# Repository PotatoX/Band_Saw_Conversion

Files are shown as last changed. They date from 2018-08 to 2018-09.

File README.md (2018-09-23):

# Band_Saw_Conversion

## Summary
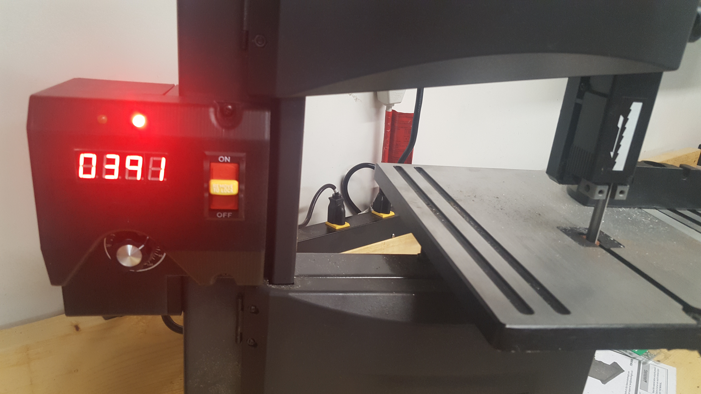
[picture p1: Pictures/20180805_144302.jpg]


Recently I needed (had an excuse to get) a band saw capable of cutting metal for a few of my projects. As with most of my projects/hobbies there are a number of outcomes I seek:

* Cheap
* Technical
* Build
* Learn

To this end I started shopping around to acquire a band saw as cheap as possible as it would only be used on a limited basis for hobby work. I need the saw to be able to cut metal and fit a small foot print on my bench. I wanted the saw to be vertical in order to minimize the space consumed as my bench and garage space is at a premium at this point.

With these constraints in mind I set my sights on a Harbor Freight 1/3 HP 9 in Benchtop Band Saw. I caught it on sale a Harbor Freight (w/ coupon) for right around $100. Similar saws can be found at your local big box stores.

Using this basic frame and some upgrades I have been able to convert this wood cutting vertical band saw to a metal cutting type with speed control and FPS display.

I now have a small band saw capable of cutting metal, wood, plastic, etc. that fits on the corner of my bench.

This project encompass the conversion and in indented to share the process with other makers. If you have questions, need additional details, or see any bugs please let me know.

The entire project can be found on [GitHub](https://github.com/PotatoX/Band_Saw_Conversion/). Consider contributing and making it even better if you happen to create other customizations.

Additionally, I will list parts used in this project on my [OpenBazzar store](https://openbazaar.com/store/QmVFRGwApdcef56Be7FPXnXQaB79rYrve3otFsrWvSwbAu).

## Design Choices
Thnking ack thrpugh the steps taken from the begining to end; a text book design process was not followed, rather a development and refine!emt from blade to display.

### The Blade
There the first choice was to find a blade that fit and was capable of cutting metalss (steel). By default the saw comes equiped woth a wood cutting 62in blade, carbon steel, 7 Teeth per Inch (*TPI*), 1/8in wide. I had found a couple of reports online that indicate success cutting plastic and aluminium, so long as a gentle touch was used. clearly the default blade had no chance of taking on steels.

Therefore the search began for a suitable bimetal blade. Most of my local stores carried various blades, some bimetal, but none in the 62in size. 62in appears to be a bit of a *custom* size. when local stores fail Amazon.com often saves the day. After scrolling though lists of blades I was able to to find a suitable blade; 62in, bimetal, 1/2in, 14 TPI.

[Imachinist S621214 62-inch X 1/2-inch X 14 TPI Bi-metal Band Saw Blades](https://www.amazon.com/gp/product/B010G9IJG6)

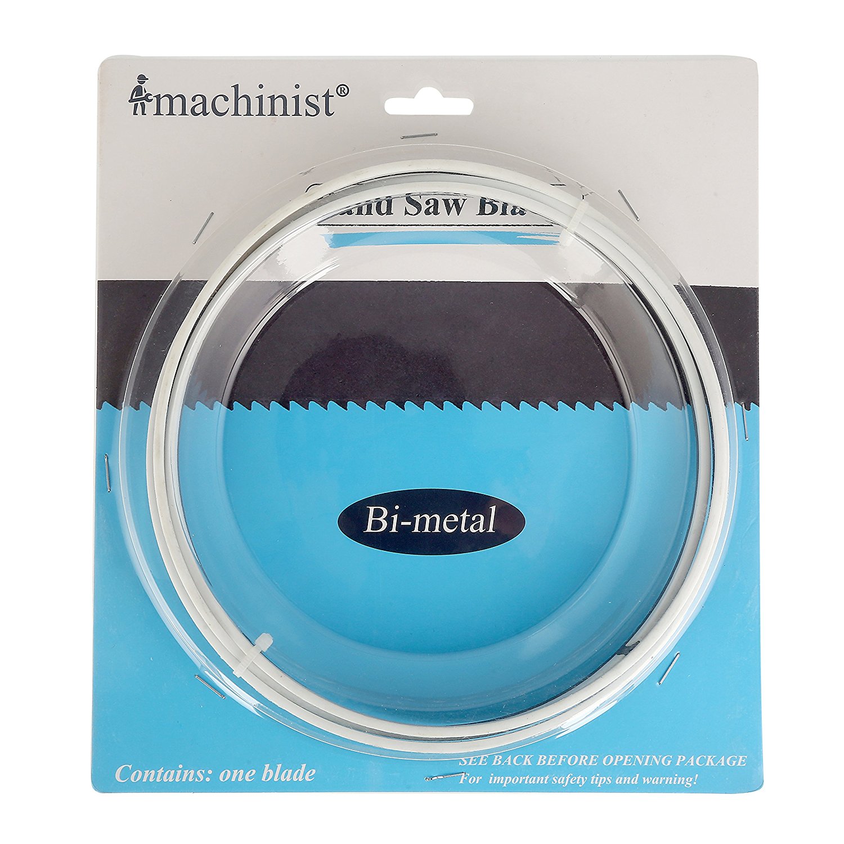
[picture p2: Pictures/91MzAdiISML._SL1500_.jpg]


The next challenge was to find a way to drive the blade @ ~300 FPM for Steel, 600ish FPM for Aluminum, and 2000 FPM for Wood. Looking at the stock motor it was designed to drive the blade at 2460 FPM and is not adjustable. Further the motor is an induction motor which can not be speed controlled without a frequency drive, and even with one, would loose power proportional to the reduction in frequency; meaning at slow speeds is would lose power.

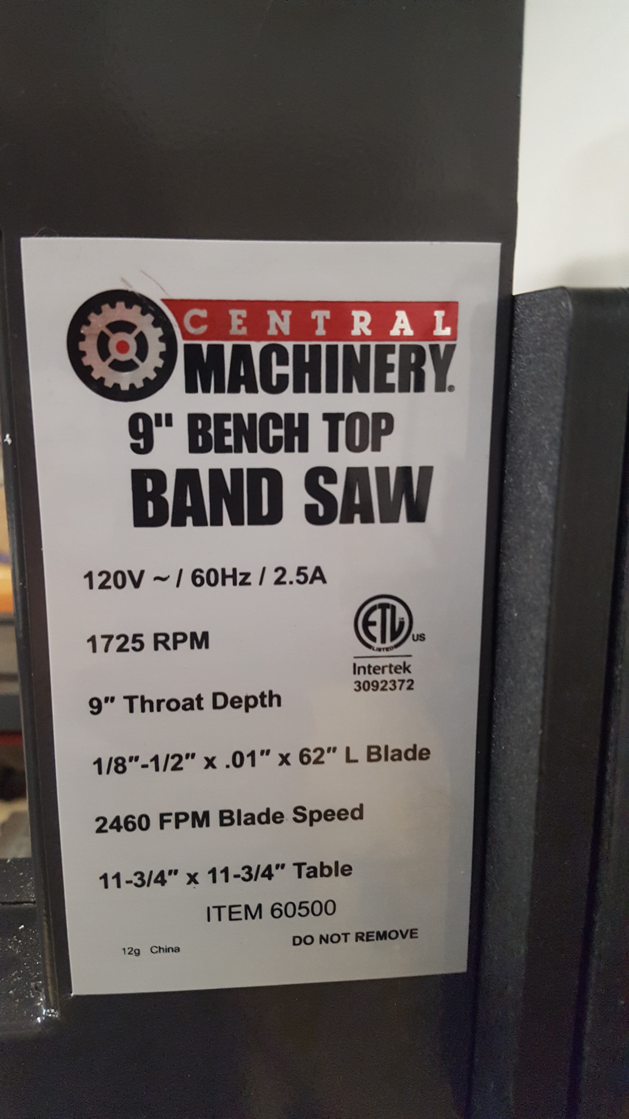
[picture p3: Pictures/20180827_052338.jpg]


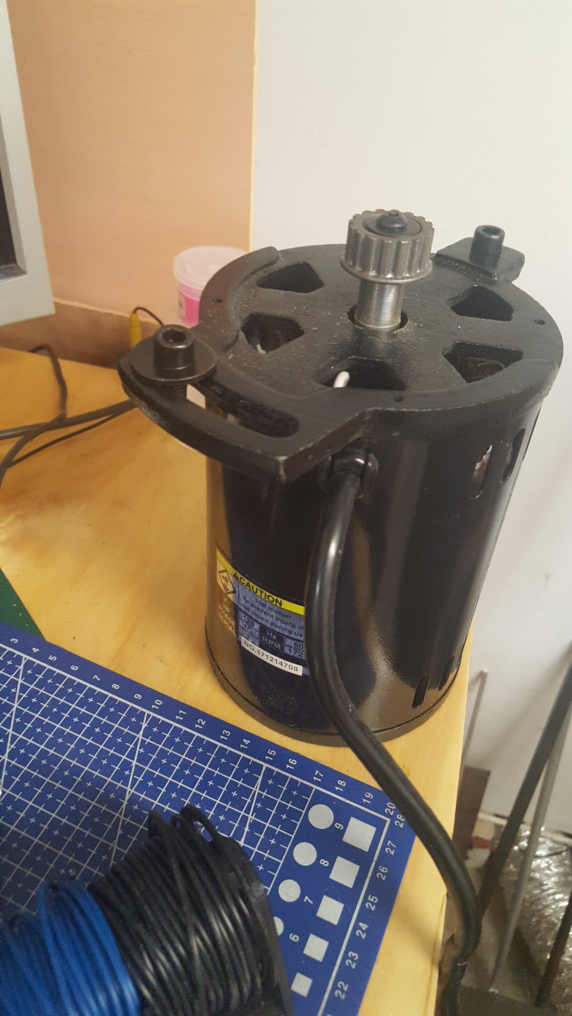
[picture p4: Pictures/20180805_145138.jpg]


Therefore, a SCR controlled DC motor setup was needed. Given the *Cheap* requirement I scrubed ebay for a cheap DC motor. I found that used DC motors from tredmills seem to be abundent and are therefore reasonably priced. I found mine for ~$30.

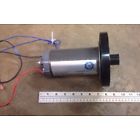
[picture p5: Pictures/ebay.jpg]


A small bracket had to be made to adapat the motor to the band saw frame

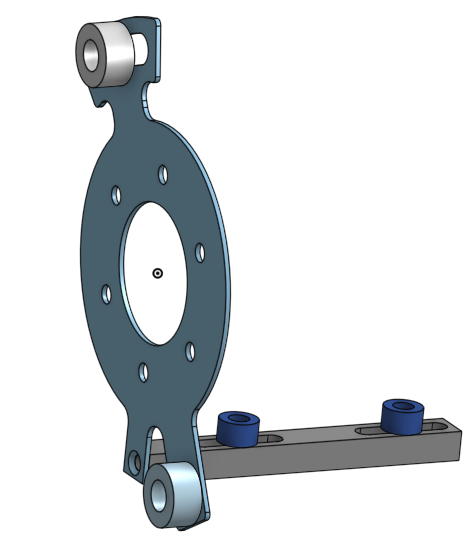
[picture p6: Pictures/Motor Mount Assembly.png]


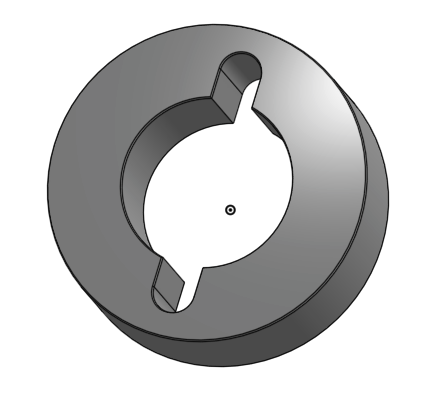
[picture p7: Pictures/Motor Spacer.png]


In order to control the motor I found a generic SCR speed control. The exact feature of the SCR were not necessary to specify other than it needed to be able to handle sufficient power. 4000W was probably over kill, but rather more than not enough, and given the price for smaller units was roughly the same, this did the trick.

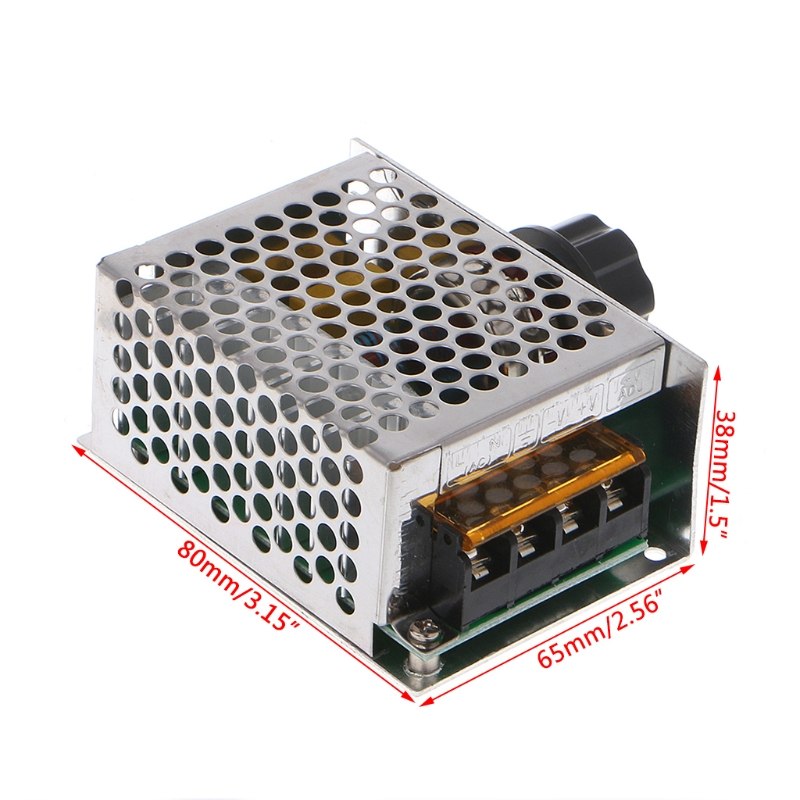
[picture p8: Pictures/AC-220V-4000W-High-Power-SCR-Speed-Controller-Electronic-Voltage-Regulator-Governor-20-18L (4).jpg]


The SCR needed a couple of mods to fine tune the upper and lower speed bounds. This is expanded on more in in the electronics section.

In order to install the motor I had a to get small belt pully mate to the motor.

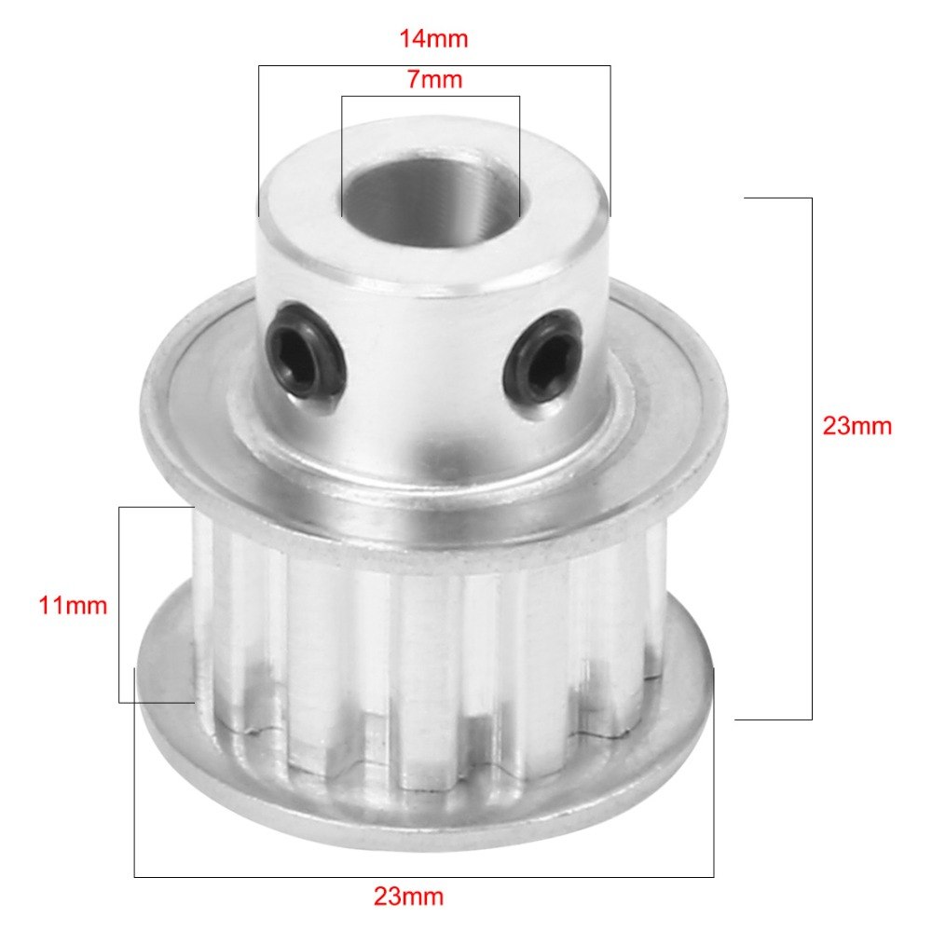
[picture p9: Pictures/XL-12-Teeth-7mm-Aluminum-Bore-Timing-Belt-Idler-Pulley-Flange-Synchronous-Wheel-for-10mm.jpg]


I then needed an clean way to mount the SCR on the frame which led to the need to design an enclosure to house and mount the SCR.

I figured, if I am going to make a custom enclosure might as well make a display to disply the FPM of the blade; I mean I've come this far, why not.

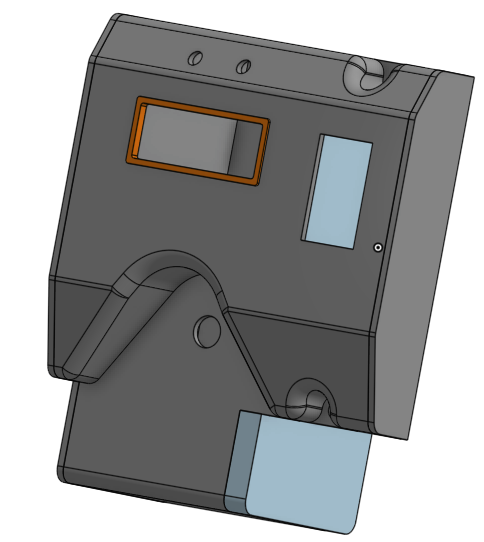
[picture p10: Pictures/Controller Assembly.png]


Lastely I designed a small board which reads a hall sensor on the back of the motor, then converts the motor shaft speed to FPM, and displays this on a small 7-Segment output. 

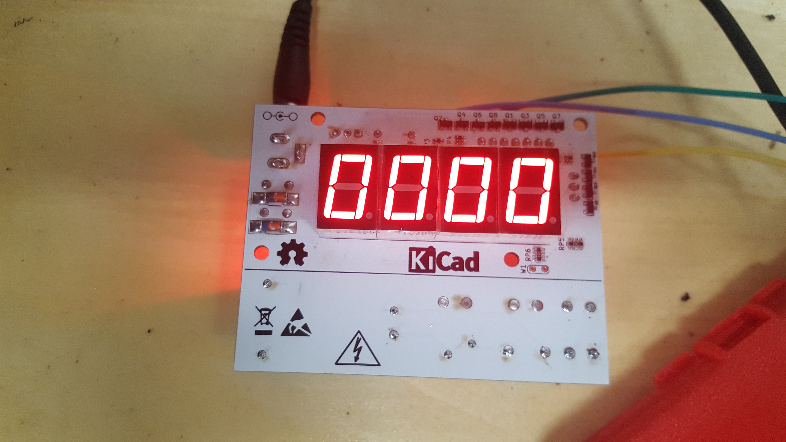
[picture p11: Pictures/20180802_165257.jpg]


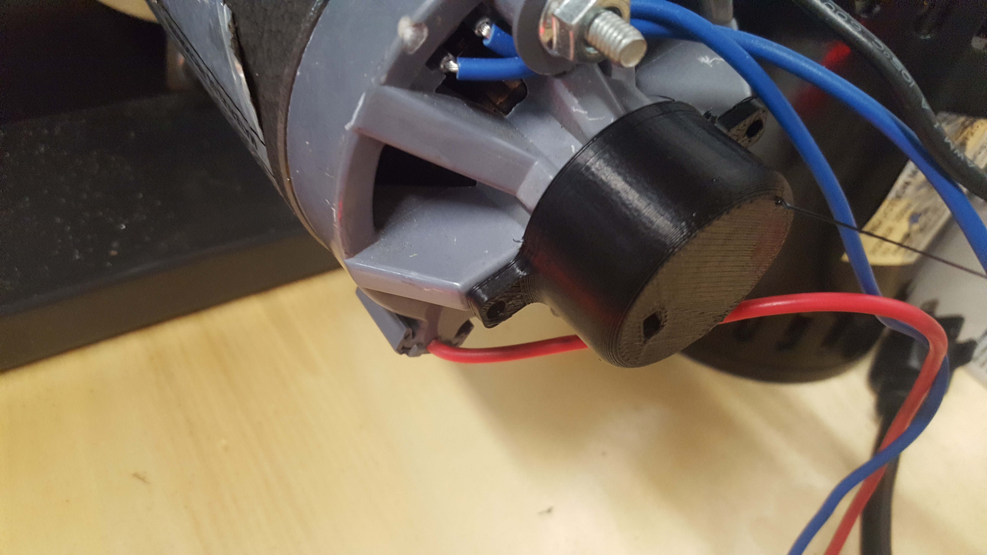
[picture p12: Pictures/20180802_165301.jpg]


## The Physical Form

### Hardware
The enclosure has been modeled in Onshape, source files can be found [here](https://cad.onshape.com/documents/ca0881e1177c075414a017b7/w/e514d8a98751ae0bca0296ff/e/90af0d38bd02678226dfc615).

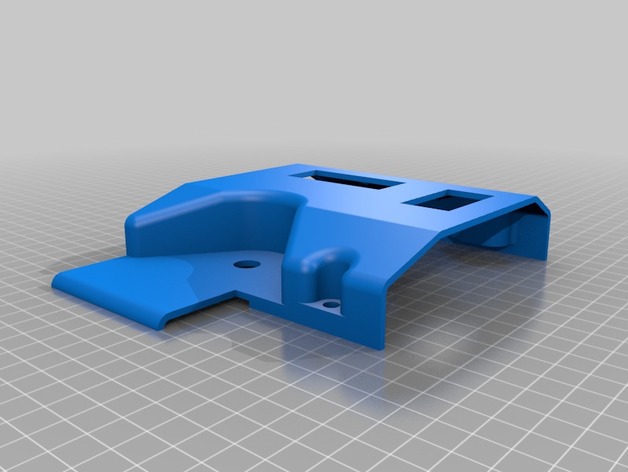
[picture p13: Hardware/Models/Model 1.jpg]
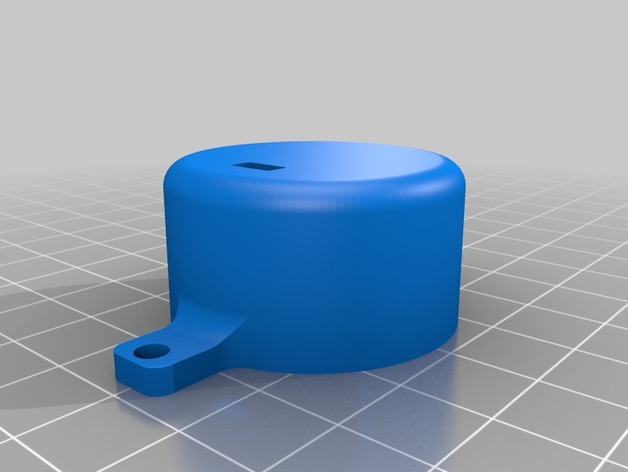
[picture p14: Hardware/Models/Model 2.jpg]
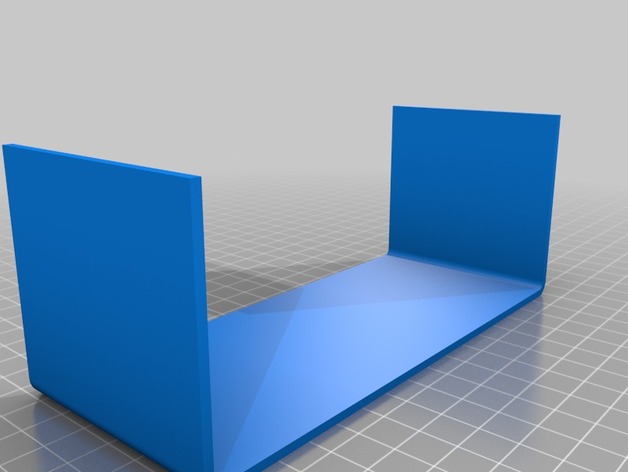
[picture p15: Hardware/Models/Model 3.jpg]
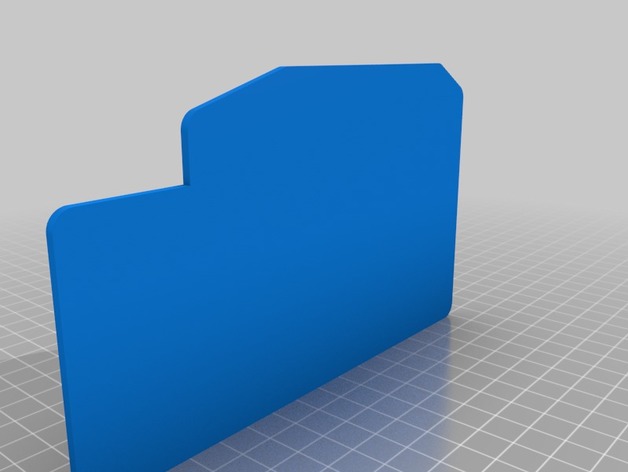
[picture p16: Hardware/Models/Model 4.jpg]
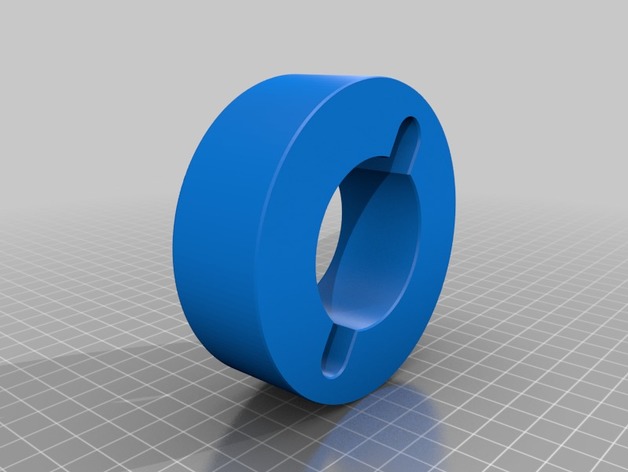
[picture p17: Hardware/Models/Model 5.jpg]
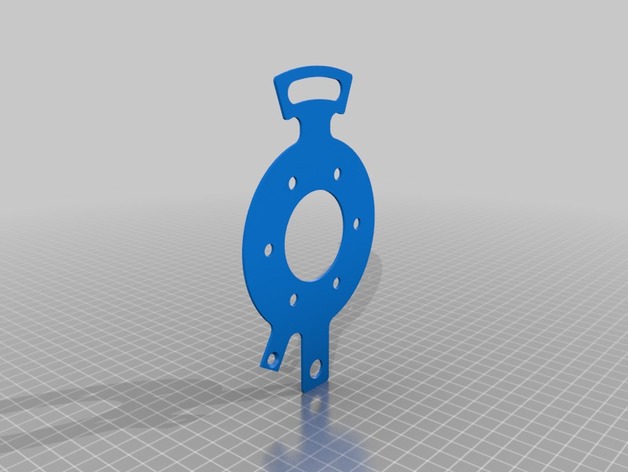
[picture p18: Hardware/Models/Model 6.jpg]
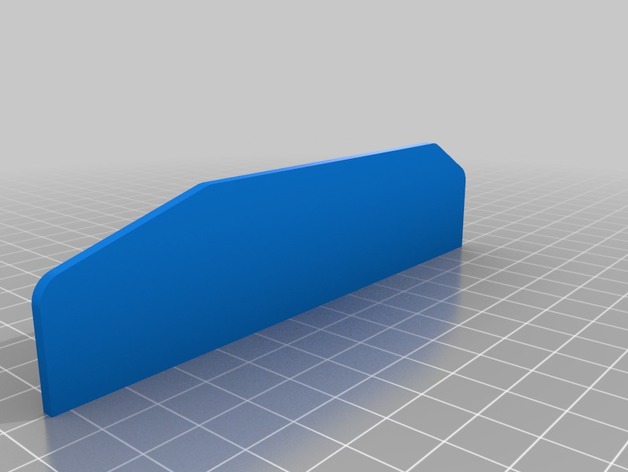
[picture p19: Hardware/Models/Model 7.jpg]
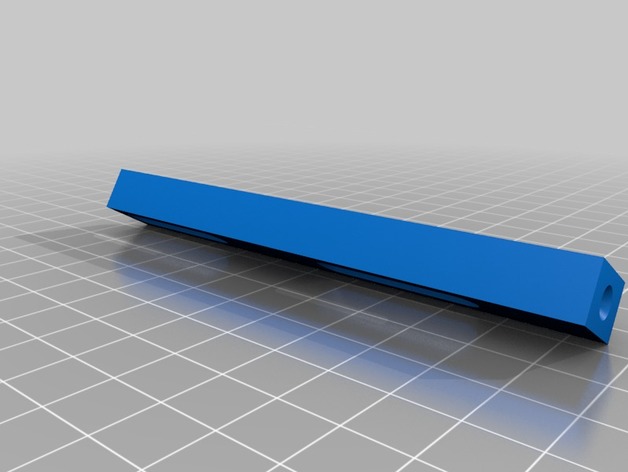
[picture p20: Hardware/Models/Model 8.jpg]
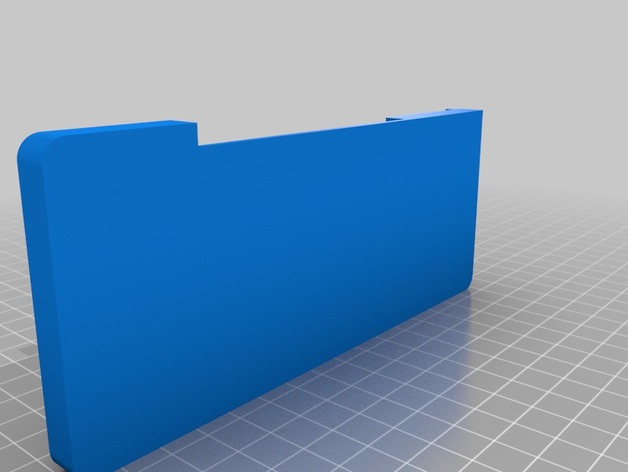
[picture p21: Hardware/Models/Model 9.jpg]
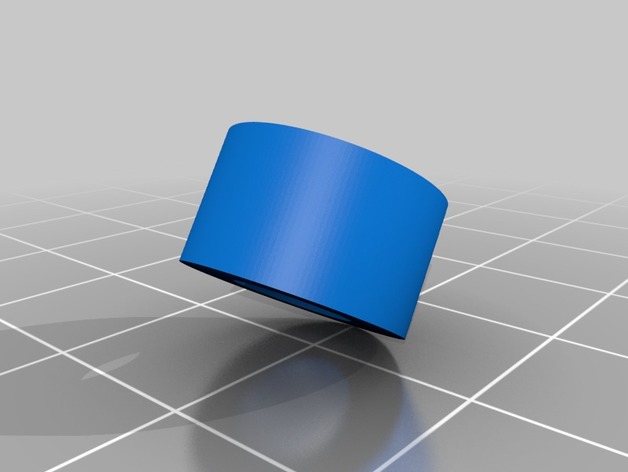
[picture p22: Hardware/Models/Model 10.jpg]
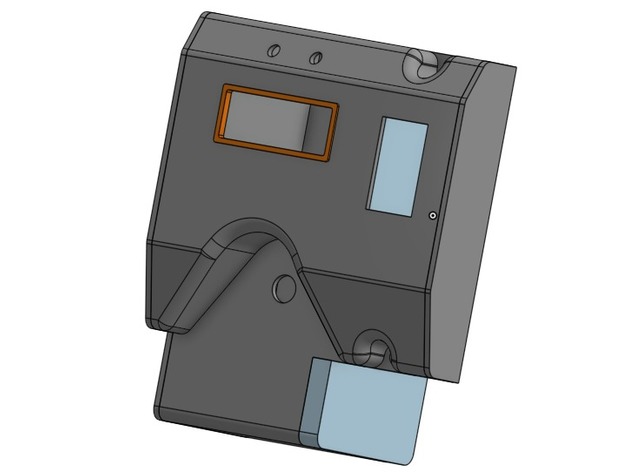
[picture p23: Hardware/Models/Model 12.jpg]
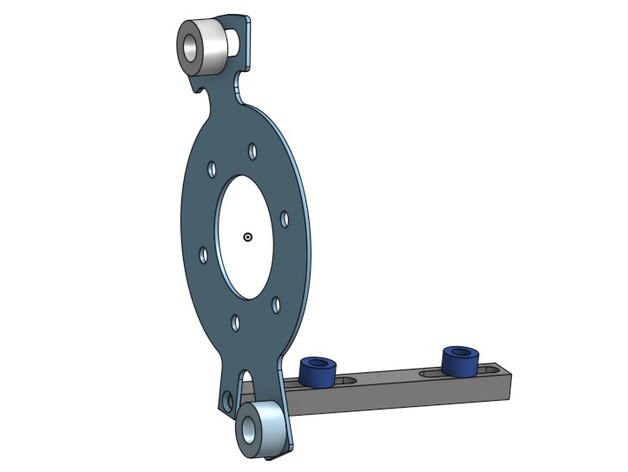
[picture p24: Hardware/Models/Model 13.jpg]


If you are in need of a 3D printed enclosure, let me know and I will be happy to add them to my [OpenBazzar store](https://openbazaar.com/store/QmVFRGwApdcef56Be7FPXnXQaB79rYrve3otFsrWvSwbAu).

### Electronics

#### SCR Modifications
Unfortunately I forgot to take pictures while modifing the SCR. If you get a generic SCR you simply have to swap out the the potentiometer some one that is of a range more appropraite for the speeds you whish to operate at. This will be SCR and motor dependent. In my case I added a 33k resistor in series with a 50K pot.

#### Hall Effect Sensor
The hall effect sensor I used was an A3141 IC. This worked for my setup given the magnet I used and its location on the rear portion of the motor shaft. Any hall effect sensor in this family should do the trick.

[Datasheet](https://github.com/PotatoX/Band_Saw_Conversion/blob/master/Electronics/KiCad/Tachometer/Datasheets/A3141-2-3-4-Datasheet.pdf)

#### Tachometer Board
The design has been complete in KiCad. Input either 120V AC or 6V-12V DC. Board can be but down to remove AC section if DC is used. I have excess boards that will be listed on my [OpenBazzar store](https://openbazaar.com/store/QmVFRGwApdcef56Be7FPXnXQaB79rYrve3otFsrWvSwbAu) along with some of the odd components.



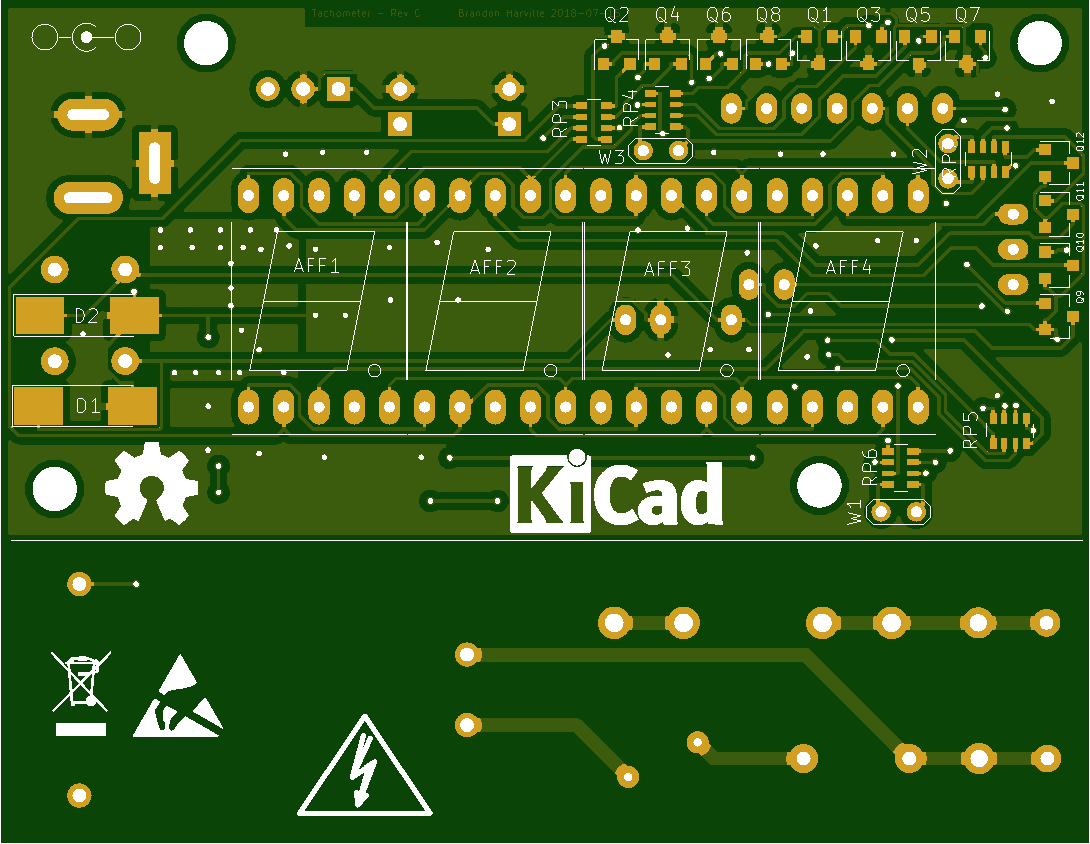
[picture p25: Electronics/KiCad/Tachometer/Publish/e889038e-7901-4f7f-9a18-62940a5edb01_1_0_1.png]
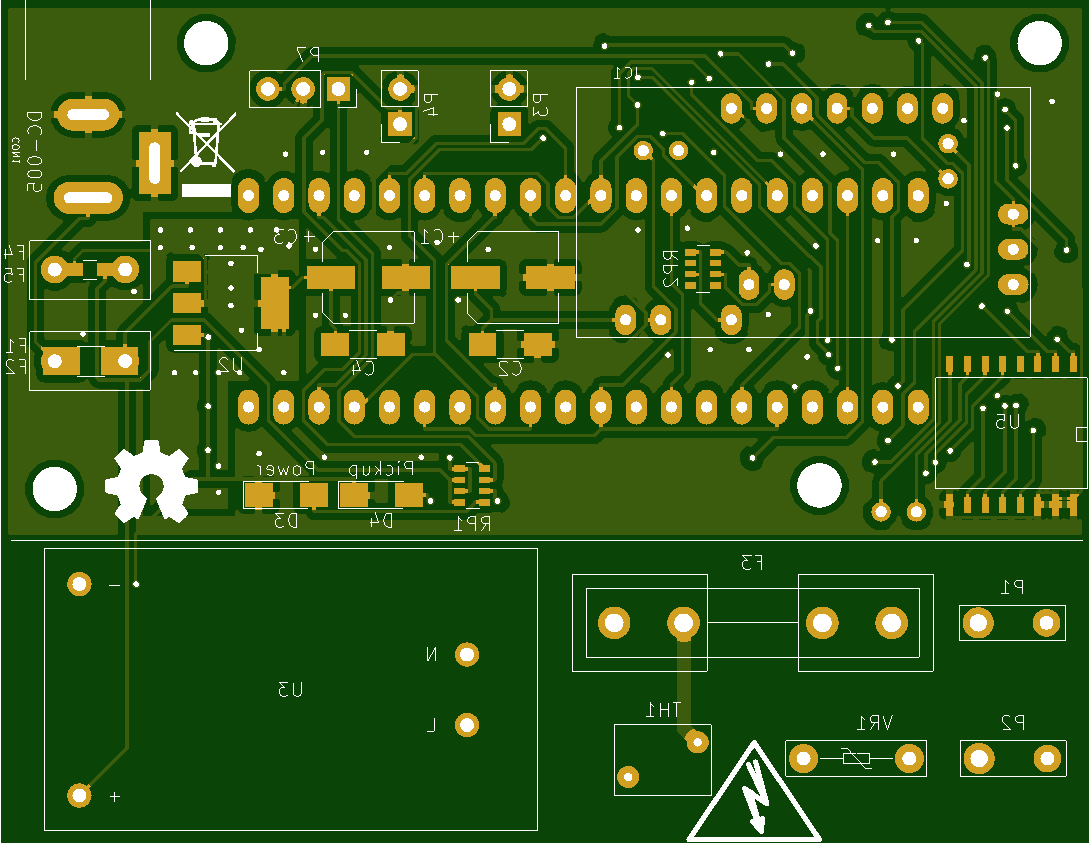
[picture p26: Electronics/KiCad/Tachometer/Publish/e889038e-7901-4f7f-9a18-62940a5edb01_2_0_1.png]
 

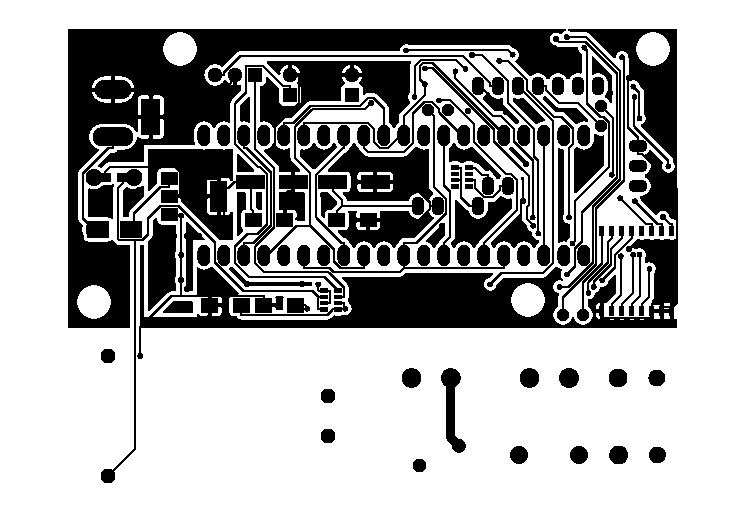
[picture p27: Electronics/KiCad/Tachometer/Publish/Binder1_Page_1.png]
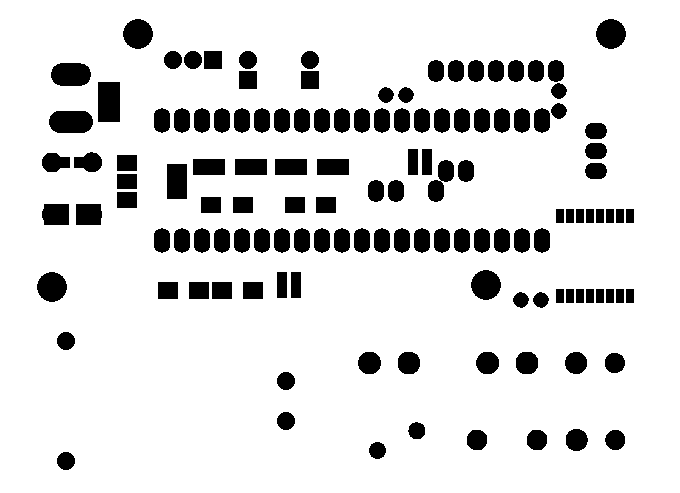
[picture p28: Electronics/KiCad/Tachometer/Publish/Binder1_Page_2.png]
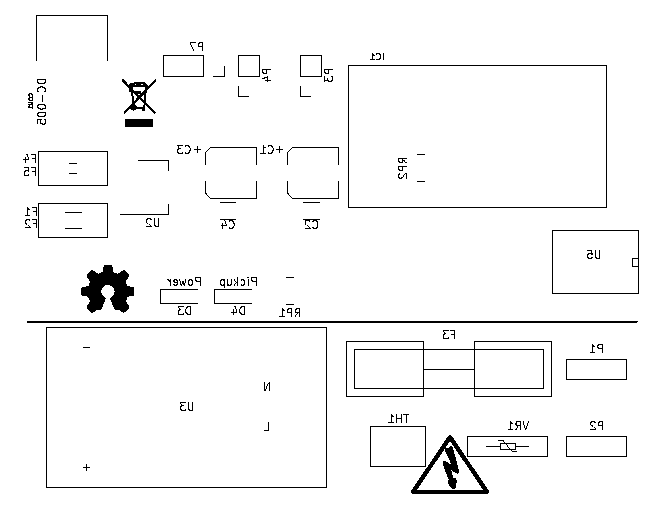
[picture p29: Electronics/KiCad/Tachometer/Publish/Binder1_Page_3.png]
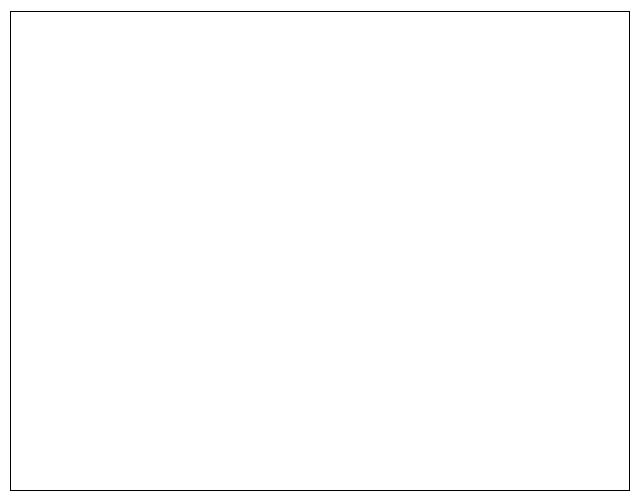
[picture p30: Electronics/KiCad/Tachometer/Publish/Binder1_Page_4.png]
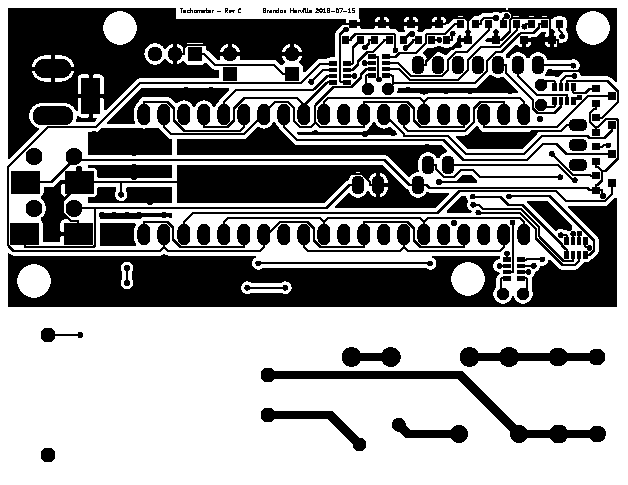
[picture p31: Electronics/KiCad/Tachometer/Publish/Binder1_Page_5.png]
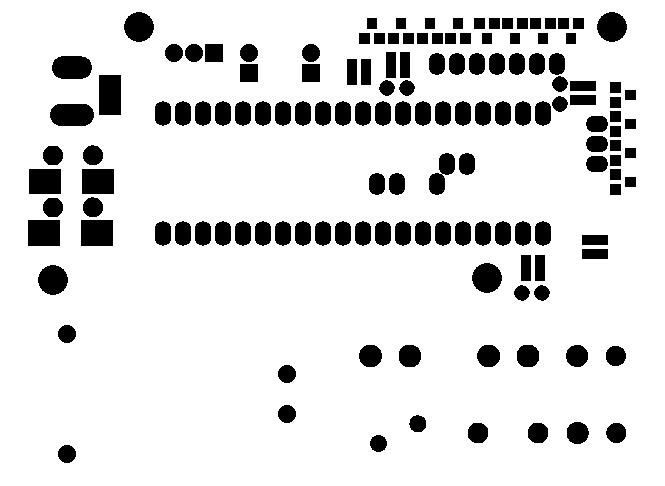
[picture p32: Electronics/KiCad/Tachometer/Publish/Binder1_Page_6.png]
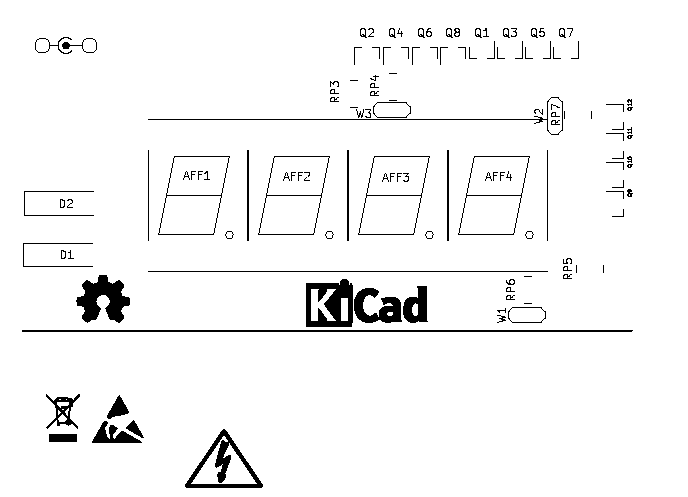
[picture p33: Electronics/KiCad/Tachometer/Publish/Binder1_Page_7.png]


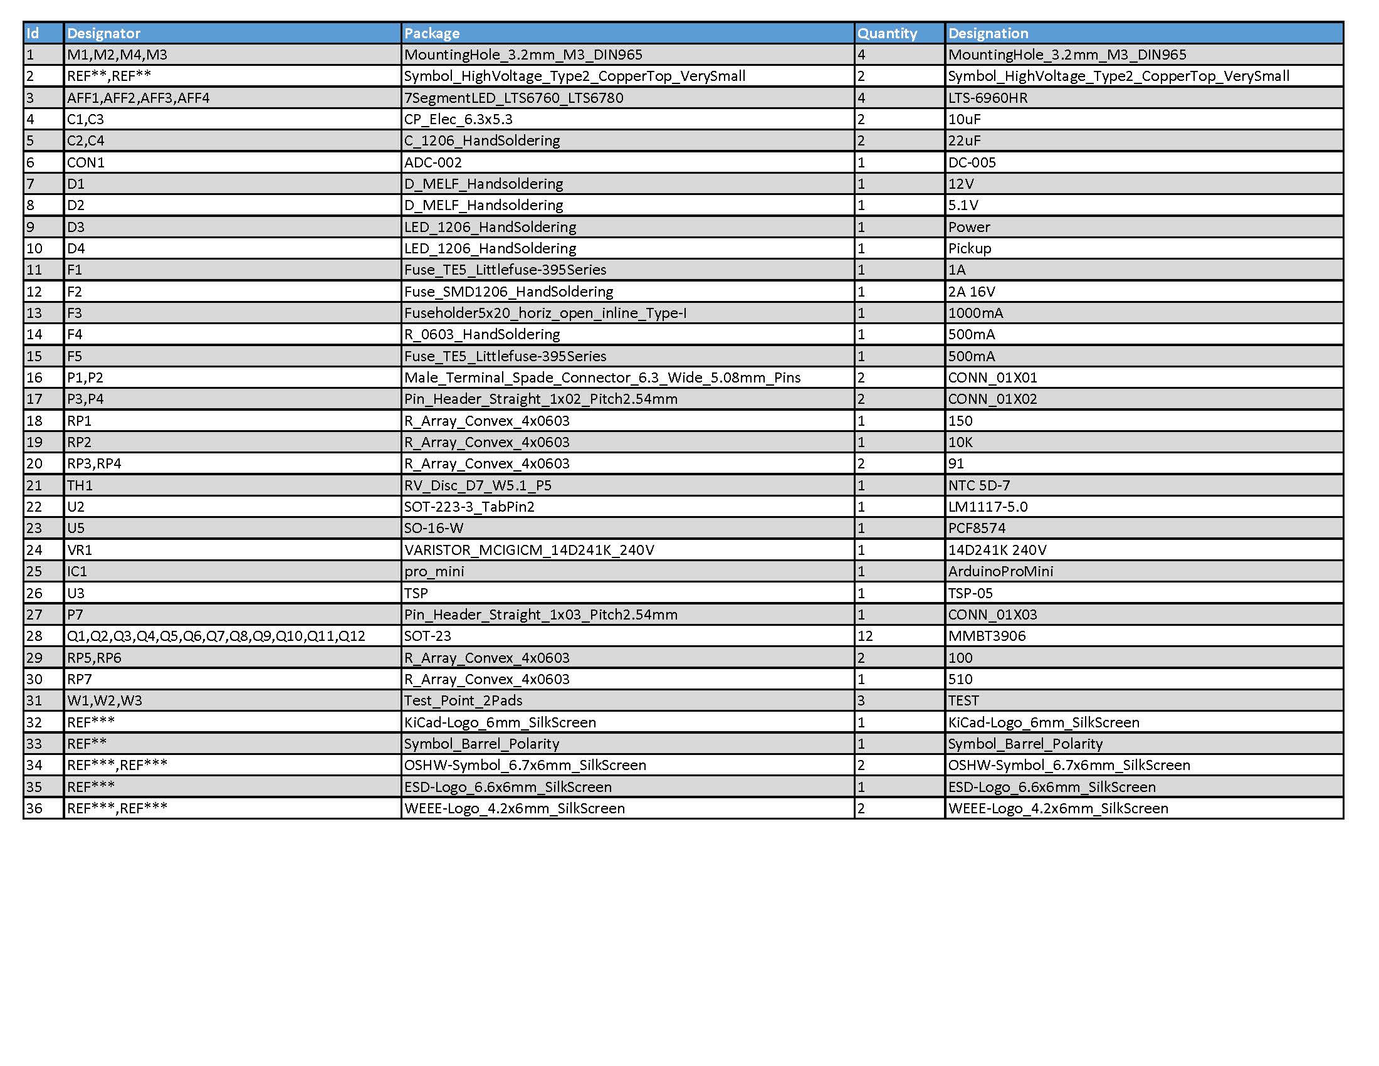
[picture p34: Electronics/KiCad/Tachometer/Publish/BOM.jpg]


If you need a component not currently listed, let me know and I will be happy to add them to my [OpenBazzar store](https://openbazaar.com/store/QmVFRGwApdcef56Be7FPXnXQaB79rYrve3otFsrWvSwbAu) along with some of the odd components..

### Software
[Arduino firmware can be found here.](https://github.com/PotatoX/Band_Saw_Conversion/tree/master/Software/Arduino/Tachometer_Rev_A)

#### Calculation of Slope
There are a couple of ways to calculate the correct [slope value](https://github.com/PotatoX/Band_Saw_Conversion/blob/c9c9d59a0e278d77ea138ab6ab9a776811436fa7/Software/Arduino/Tachometer_Rev_A/Tachometer_Rev_A.ino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) for the firmware:

##### Method 1 - Experimentation w/ Tachometer
This method requires a [contactless tachometer](https://www.aliexpress.com/item/2017-Hot-Selling-NEW-Digital-Laser-Photo-Tachometer-Non-Contact-RPM-Tach-Speed-Gauge-Engine-High/32827623720.html).

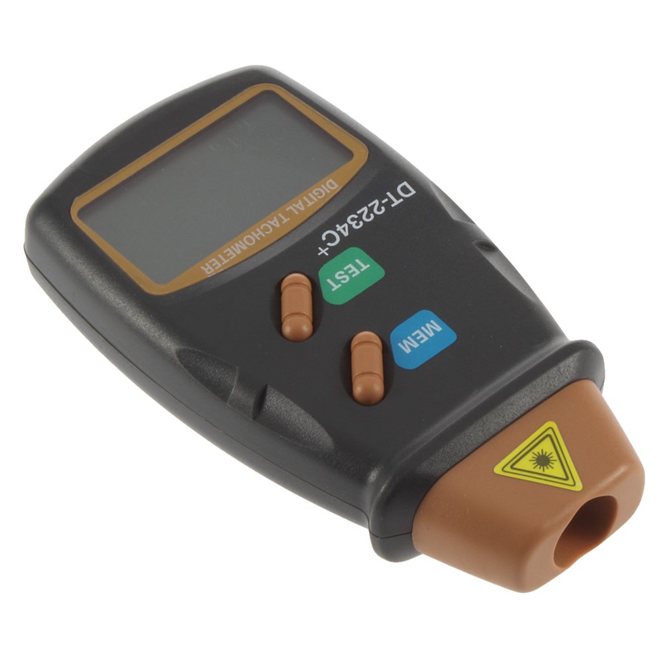
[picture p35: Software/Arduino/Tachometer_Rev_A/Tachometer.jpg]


1. Initially set the slope to 1 and flash the controller.
2. Connect the controller board to the saw and verify proper operation
3. Measure the diameter of one of your blade drive wheels.
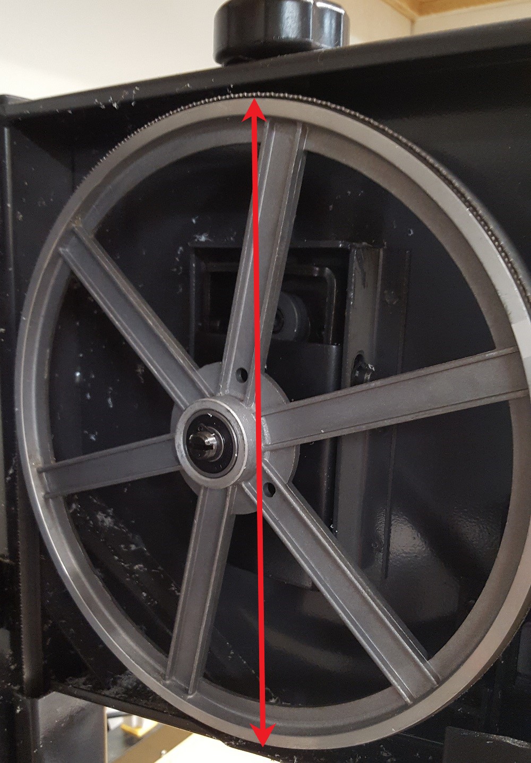
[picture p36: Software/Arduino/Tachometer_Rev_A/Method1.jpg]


4. Place a tachometer reflector on the blade drive wheel and test that stable RPM readings can be taken. **DANGER - _As the cover to the saw is open in order to take this measurement take extream care to be as far away from the blade as possible, and allow yourself multiple options for escape and power shut off incase the blade should come off the drive wheels._**
5. Start the band saw at a low speed and record both the reading on the controller and the reading on the tachometer.
6. Repeat measurements various times in order to take readings through out the intended operating speed range.
7. Using a [spreadsheet](https://github.com/PotatoX/Band_Saw_Conversion/blob/master/Software/Arduino/Tachometer_Rev_A/BandSaw%20Slope%20Calculations.ods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) convert the tachometer readings to SFM
8. Using a [spreadsheet](https://github.com/PotatoX/Band_Saw_Conversion/blob/master/Software/Arduino/Tachometer_Rev_A/BandSaw%20Slope%20Calculations.ods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) plot the controller readings vs the SFM(tachometer readings).
10. Generate a linear fit, note the slope of the fit equation.
11. Input the slope into the firmware of the controller and re-flash. The controller should now read in SFM.

##### Method 2 - Ratio Calculations
1. Measure the diameter of one of your blade drive wheels.
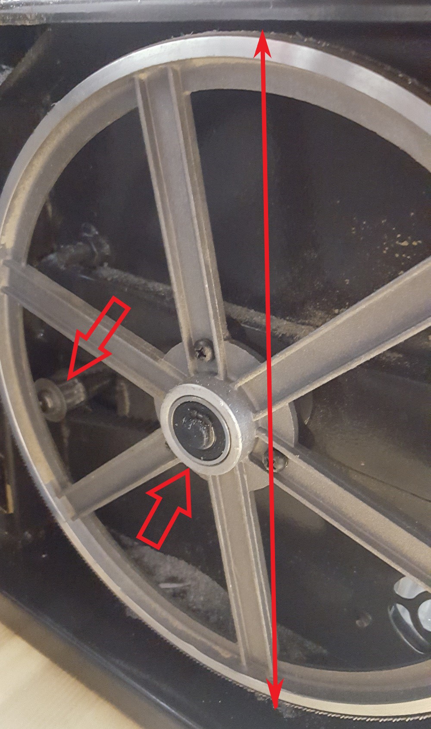
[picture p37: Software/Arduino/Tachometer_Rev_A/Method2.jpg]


2. Count the teeth of the motor pully and the blade wheel pully.
3. Enter the all values in the [spreadsheet](https://github.com/PotatoX/Band_Saw_Conversion/blob/master/Software/Arduino/Tachometer_Rev_A/BandSaw%20Slope%20Calculations.ods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).
4. Input the slope into the firmware of the controller and flash. The controller should now read in SFM.

# Support Projects Like This
You can support projects like this by using my [OpenBazzar store](https://openbazaar.com/store/QmVFRGwApdcef56Be7FPXnXQaB79rYrve3otFsrWvSwbAu). Like all hobbies, ones that are self-funded are always easier progress.

# Safety/Disclaimer
I am furnishing this item/content "as is". I do not provide any warranty of the item/content whatsoever, whether express, implied, or statutory, including, but not limited to, any warranty of merchantability or fitness for a particular purpose or any warranty that the contents of the item/content will be error-free.

In no respect shall I incur any liability for any damages, including, but limited to, direct, indirect, special, or consequential damages arising out of, resulting from, or any way connected to the use of the item, whether or not based upon warranty, contract, tort, or otherwise; whether or not injury was sustained by persons or property or otherwise; and whether or not loss was sustained from, or arose out of, the results of, the item/content, or any services that may be provided herein.

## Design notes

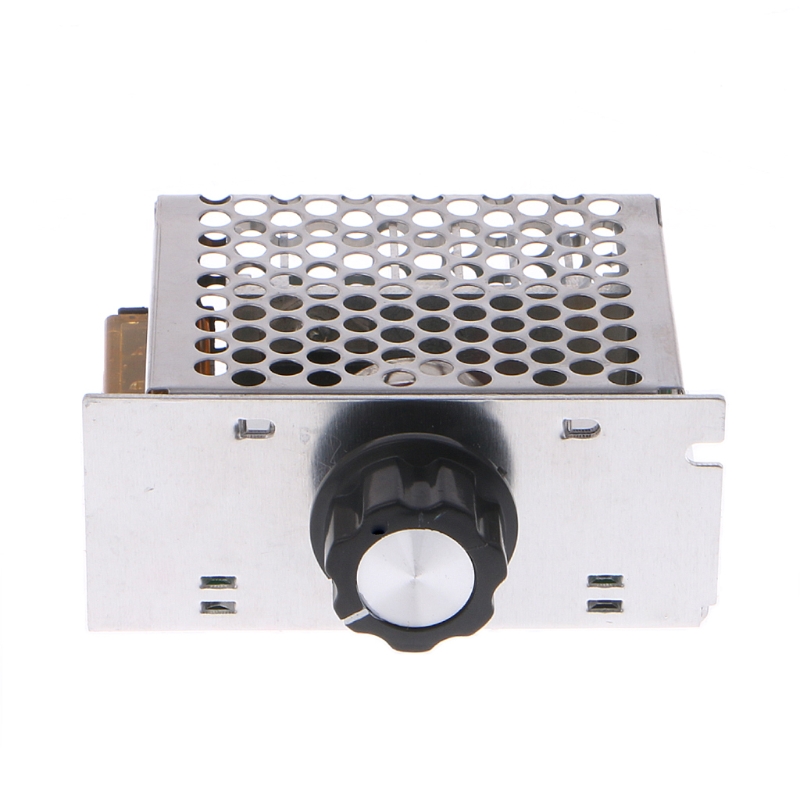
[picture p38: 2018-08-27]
Pictures/AC-220V-4000W-High-Power-SCR-Speed-Controller-Electronic-Voltage-Regulator-Governor-20-18L (2).jpg

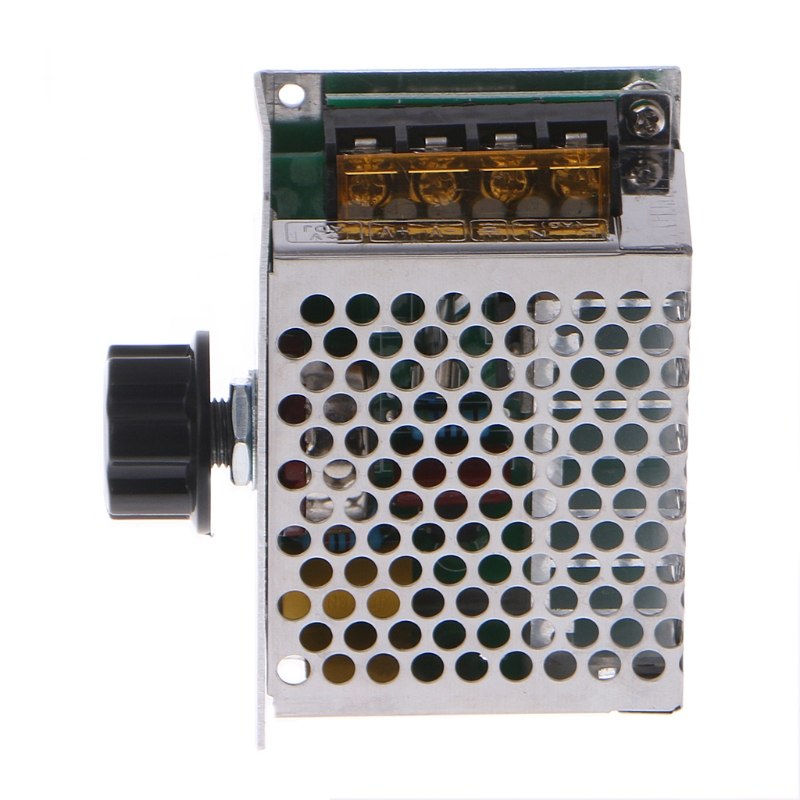
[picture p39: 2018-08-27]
Pictures/AC-220V-4000W-High-Power-SCR-Speed-Controller-Electronic-Voltage-Regulator-Governor-20-18L (3).jpg

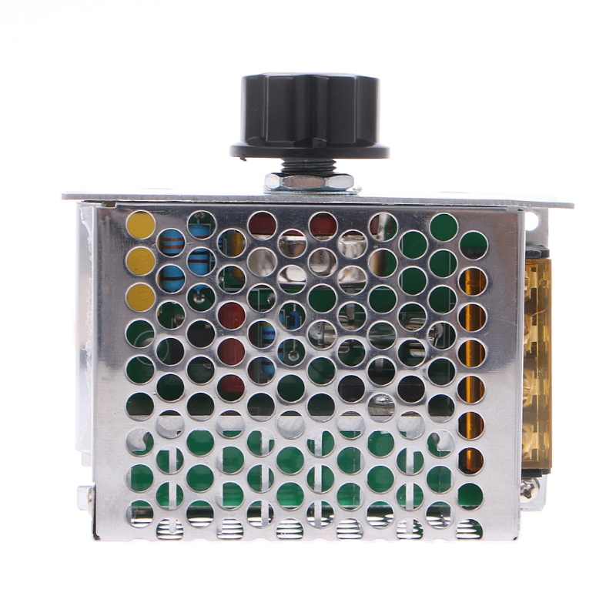
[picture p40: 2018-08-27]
Pictures/AC-220V-4000W-High-Power-SCR-Speed-Controller-Electronic-Voltage-Regulator-Governor-20-18L.jpg

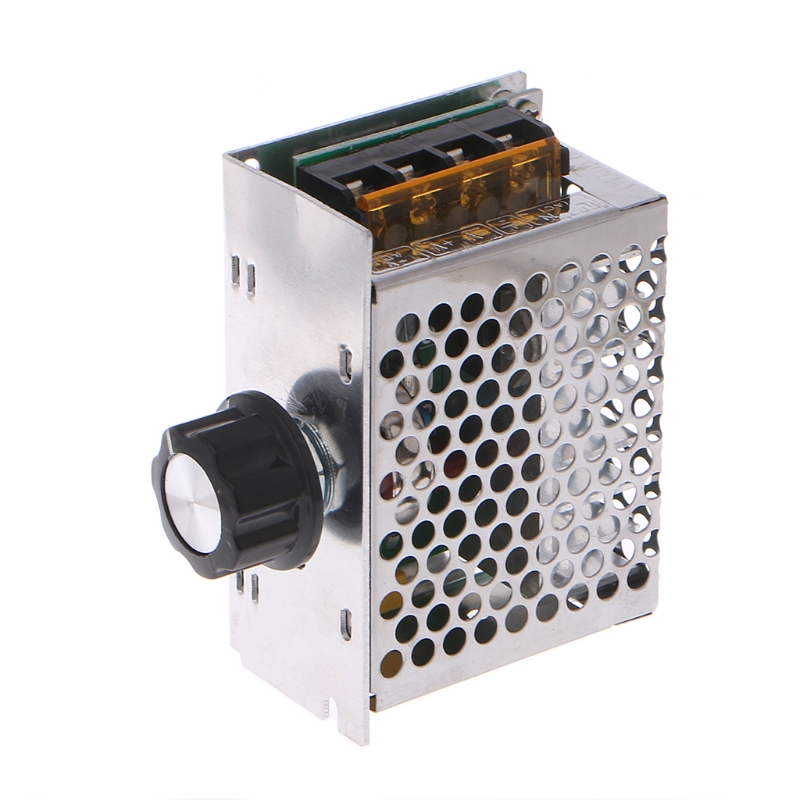
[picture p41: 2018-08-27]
Pictures/AC-220V-4000W-High-Power-SCR-Speed-Controller-Electronic-Voltage-Regulator-Governor-20-18L (1).jpg

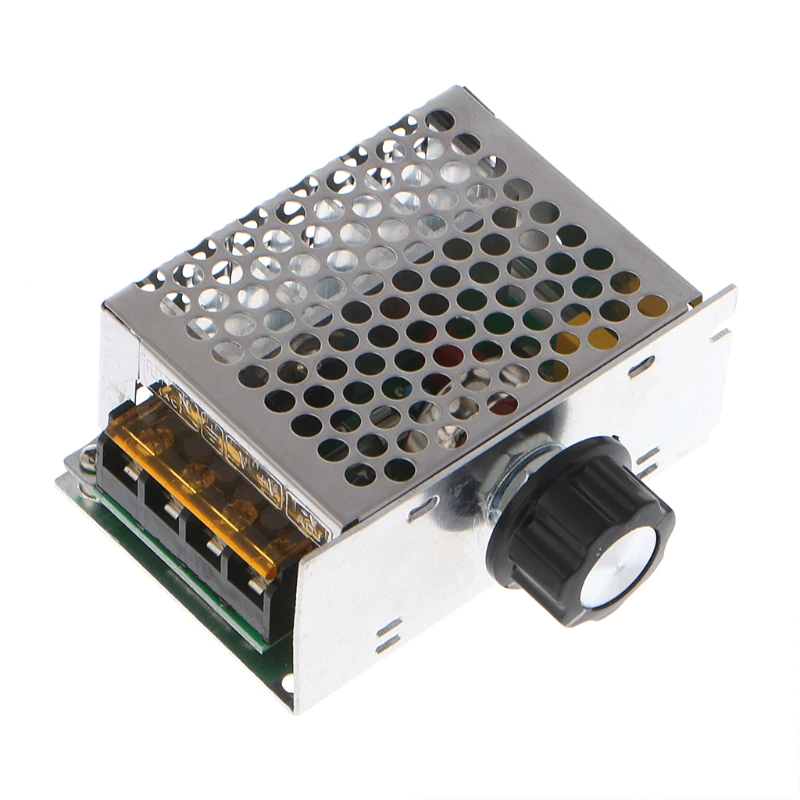
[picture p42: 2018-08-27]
Pictures/AC-220V-4000W-High-Power-SCR-Speed-Controller-Electronic-Voltage-Regulator-Governor-20-18L (5).jpg

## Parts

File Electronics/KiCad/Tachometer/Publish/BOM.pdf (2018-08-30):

Id | Designator | Package | Quantity | Designation
1 | M1,M2,M4,M3 | MountingHole_3.2mm_M3_DIN965 | 4 | MountingHole_3.2mm_M3_DIN965
2 | REF**,REF** | Symbol_HighVoltage_Type2_CopperTop_VerySmall | 2 | Symbol_HighVoltage_Type2_CopperTop_VerySmall
3 | AFF1,AFF2,AFF3,AFF4 | 7SegmentLED_LTS6760_LTS6780 | 4 | LTS-6960HR
4 | C1,C3 | CP_Elec_6.3x5.3 | 2 | 10uF
5 | C2,C4 | C_1206_HandSoldering | 2 | 22uF
6 | CON1 | ADC-002 | 1 | DC-005
7 | D1 | D_MELF_Handsoldering | 1 | 12V
8 | D2 | D_MELF_Handsoldering | 1 | 5.1V
9 | D3 | LED_1206_HandSoldering | 1 | Power
10 | D4 | LED_1206_HandSoldering | 1 | Pickup
11 | F1 | Fuse_TE5_Littlefuse-395Series | 1 | 1A
12 | F2 | Fuse_SMD1206_HandSoldering | 1 | 2A 16V
13 | F3 | Fuseholder5x20_horiz_open_inline_Type-I | 1 | 1000mA
14 | F4 | R_0603_HandSoldering | 1 | 500mA
15 | F5 | Fuse_TE5_Littlefuse-395Series | 1 | 500mA
16 | P1,P2 | Male_Terminal_Spade_Connector_6.3_Wide_5.08mm_Pins | 2 | CONN_01X01
17 | P3,P4 | Pin_Header_Straight_1x02_Pitch2.54mm | 2 | CONN_01X02
18 | RP1 | R_Array_Convex_4x0603 | 1 | 150
19 | RP2 | R_Array_Convex_4x0603 | 1 | 10K
20 | RP3,RP4 | R_Array_Convex_4x0603 | 2 | 91
21 | TH1 | RV_Disc_D7_W5.1_P5 | 1 | NTC 5D-7
22 | U2 | SOT-223-3_TabPin2 | 1 | LM1117-5.0
23 | U5 | SO-16-W | 1 | PCF8574
24 | VR1 | VARISTOR_MCIGICM_14D241K_240V | 1 | 14D241K 240V
25 | IC1 | pro_mini | 1 | ArduinoProMini
26 | U3 | TSP | 1 | TSP-05
27 | P7 | Pin_Header_Straight_1x03_Pitch2.54mm | 1 | CONN_01X03
28 | Q1,Q2,Q3,Q4,Q5,Q6,Q7,Q8,Q9,Q10,Q11,Q12 | SOT-23 | 12 | MMBT3906
29 | RP5,RP6 | R_Array_Convex_4x0603 | 2 | 100
30 | RP7 | R_Array_Convex_4x0603 | 1 | 510
31 | W1,W2,W3 | Test_Point_2Pads | 3 | TEST
32 | REF*** | KiCad-Logo_6mm_SilkScreen | 1 | KiCad-Logo_6mm_SilkScreen
33 | REF** | Symbol_Barrel_Polarity | 1 | Symbol_Barrel_Polarity
34 | REF***,REF*** | OSHW-Symbol_6.7x6mm_SilkScreen | 2 | OSHW-Symbol_6.7x6mm_SilkScreen
35 | REF*** | ESD-Logo_6.6x6mm_SilkScreen | 1 | ESD-Logo_6.6x6mm_SilkScreen
36 | REF***,REF*** | WEEE-Logo_4.2x6mm_SilkScreen | 2 | WEEE-Logo_4.2x6mm_SilkScreen

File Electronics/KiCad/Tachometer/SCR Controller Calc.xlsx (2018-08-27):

R1 | 104.8153647 |  |  |  |  | R1 | 43.33333334
R2 | 129.0094473
Solver |  |  |  |  |  | Solver
R1 | Rp | R2 | Total R | Target | Error | R1 | Rp | R2 | Total R | Target | Error
104.8153647 | 44 | 129.0094473 | 160.0000379 | 160 | 3.791798349e-05 | 43.33333334 | 520 | 140 | 180 | 180 | 1.530679583e-09
104.8153647 | 1 | 129.0094473 | 129.9999969 | 130 | 3.13383336e-06 | 43.33333334 | 1 | 140 | 140.9774436 | 141 | 0.02255639098
 |  |  |  | Total Err | 4.105181685e-05 |  |  |  |  | Total Err | 0.02255639251
Actual |  |  |  |  |  | Actual
R1 | Rp | R2 | Total R |  |  | R1 | Rp | R2 | Total R
105000 | 44000 | 130000 | 161006.7114 |  |  | 105000 | 44000 | 130000 | 161006.7114
105000 | 1e-06 | 130000 | 130000 |  |  | 105000 | 1e-06 | 130000 | 130000

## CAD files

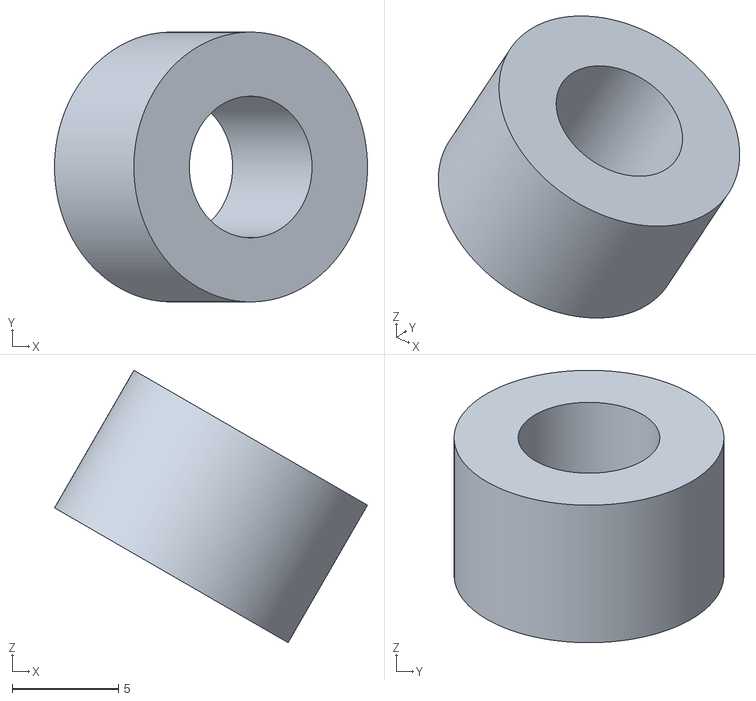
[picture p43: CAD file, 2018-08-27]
Hardware/Models/MotorMount_BandSaw - Spacer, Motor.stl
14.7 x 12.7 x 12.8

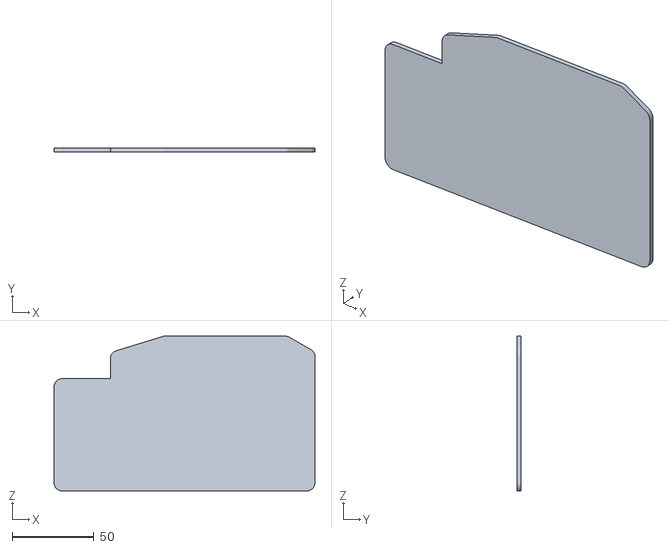
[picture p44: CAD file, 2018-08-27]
Hardware/Models/Control_Cover - Cover_1.stl
159.3 x 2.50 x 94.5

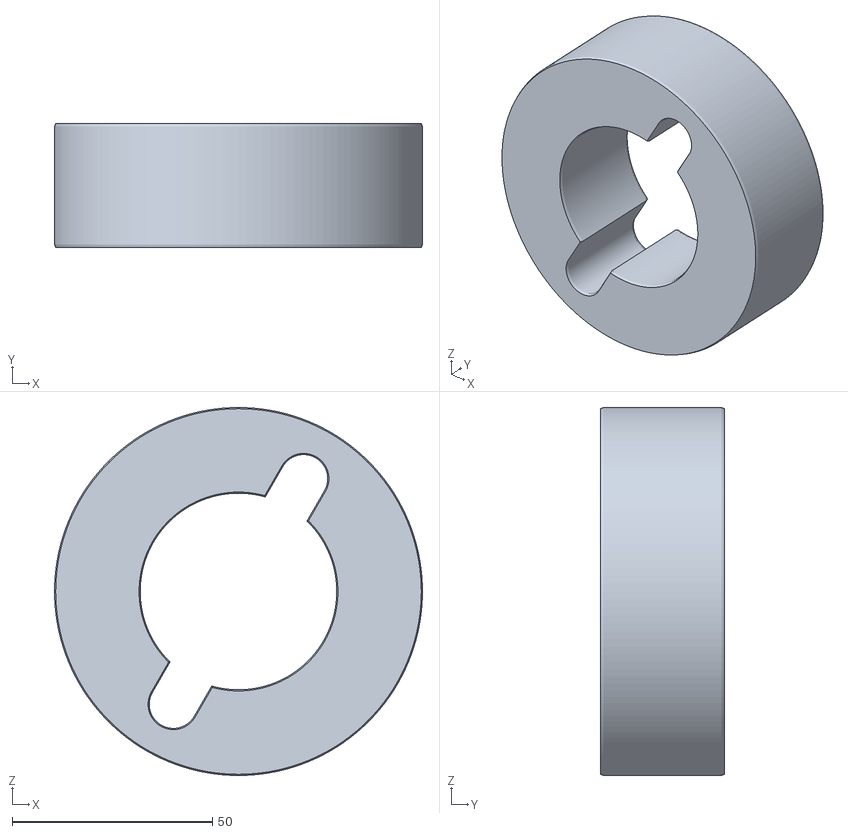
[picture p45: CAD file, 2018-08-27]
Hardware/Models/MotorMount_BandSaw_Spacer - MotorMount_BandSaw_Spacer.stl
91.8 x 31.0 x 91.8

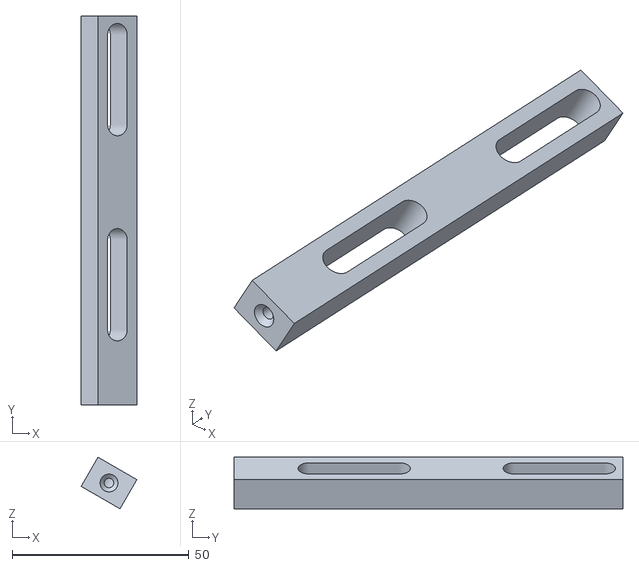
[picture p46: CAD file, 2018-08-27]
Hardware/Models/MotorMount_BandSaw - Motor_Support.stl
15.8 x 110.0 x 14.6

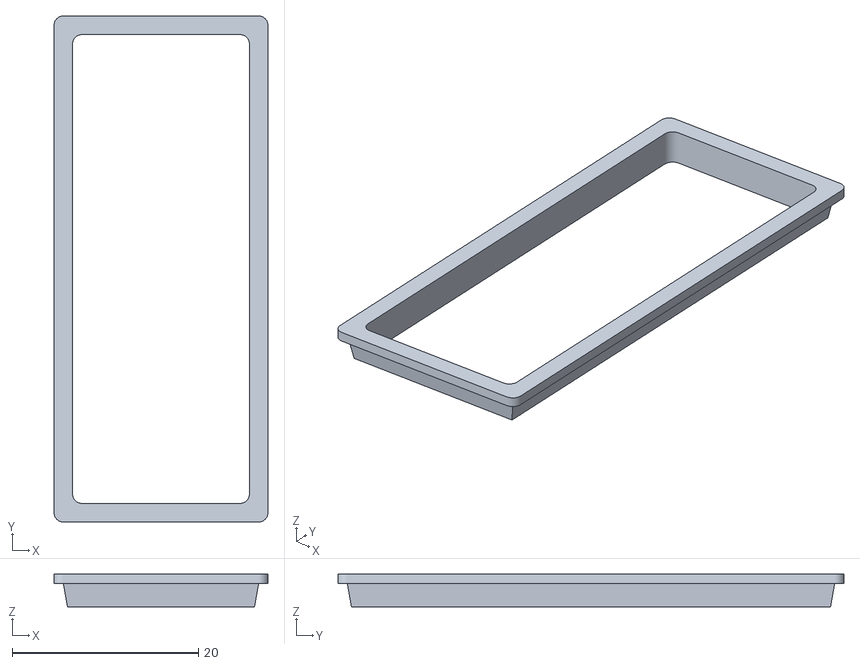
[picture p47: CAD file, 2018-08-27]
Hardware/Models/Control_Cover - Display_Frame.stl
23.0 x 54.4 x 3.50

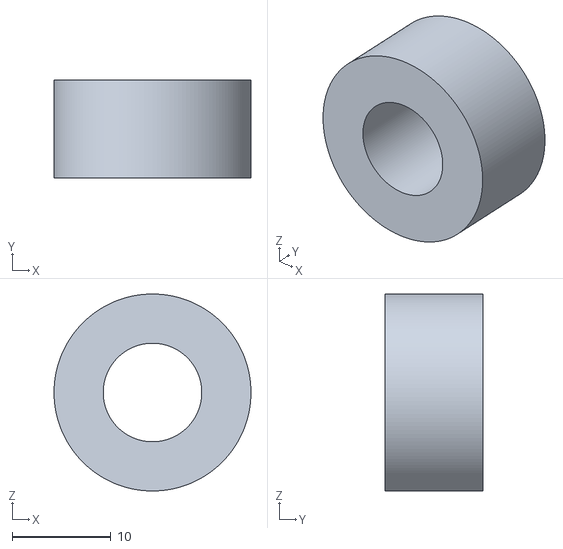
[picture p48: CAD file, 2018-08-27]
Hardware/Models/MotorMount_BandSaw - Spacer, Bracket.stl
20.0 x 10.00 x 20.0

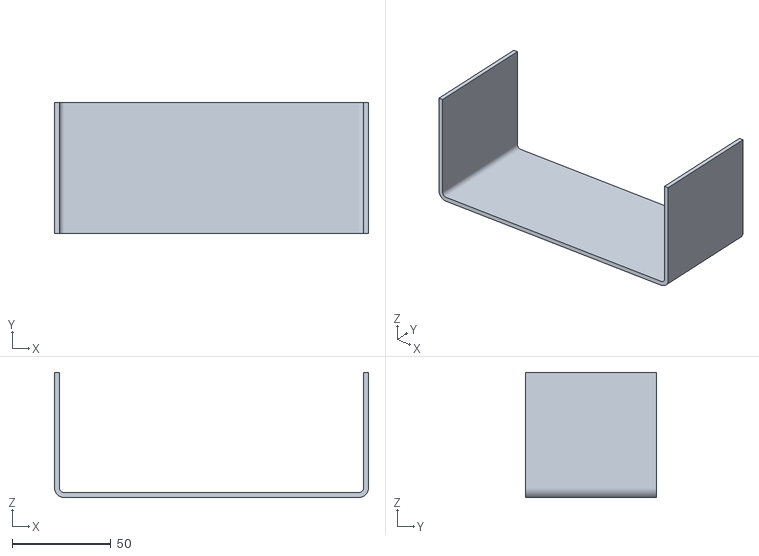
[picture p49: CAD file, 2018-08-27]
Hardware/Models/Control_Cover - Cover_2.stl
159.3 x 66.5 x 63.5

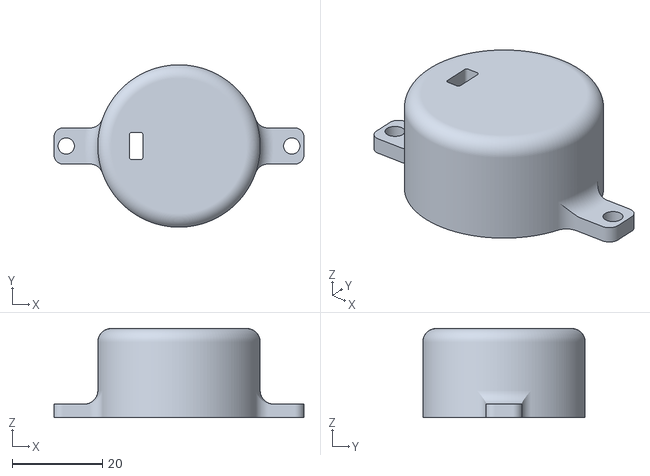
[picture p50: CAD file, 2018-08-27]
Hardware/Models/Hall_Sensor_Cap - Hall_Sensor_Cap.stl
55.4 x 36.0 x 19.8

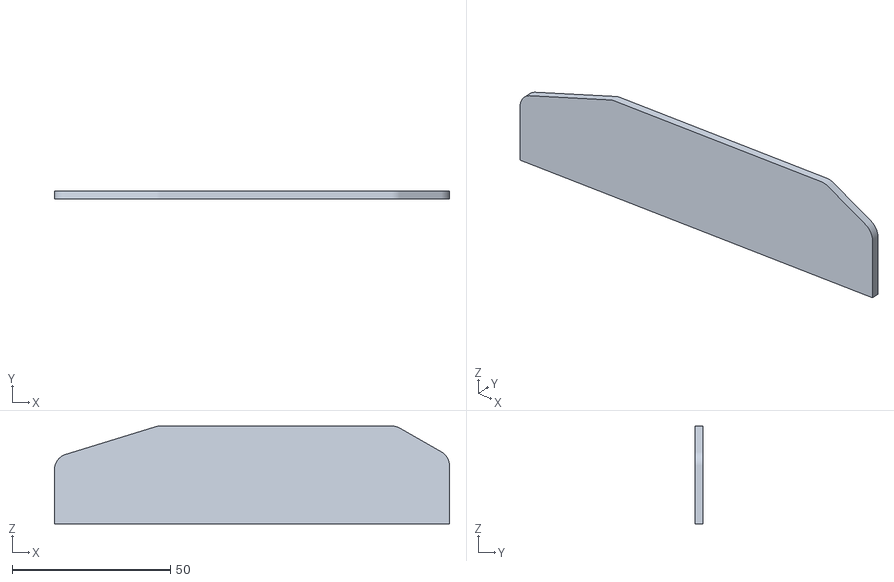
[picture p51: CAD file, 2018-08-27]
Hardware/Models/Control_Cover - Cover_3.stl
125.0 x 2.50 x 31.0

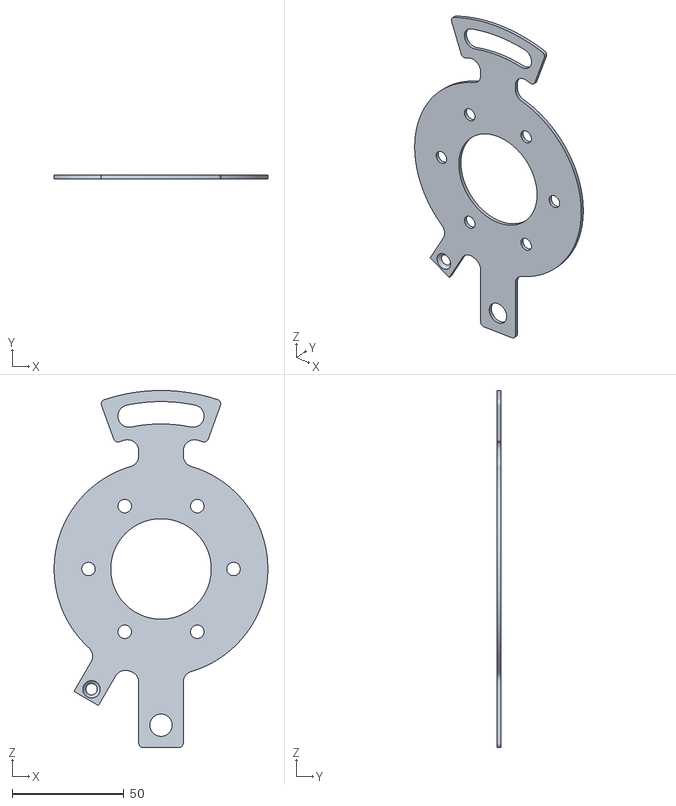
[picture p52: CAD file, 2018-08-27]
Hardware/Models/MotorMount_BandSaw - Bracket.stl
95.8 x 1.59 x 160.0

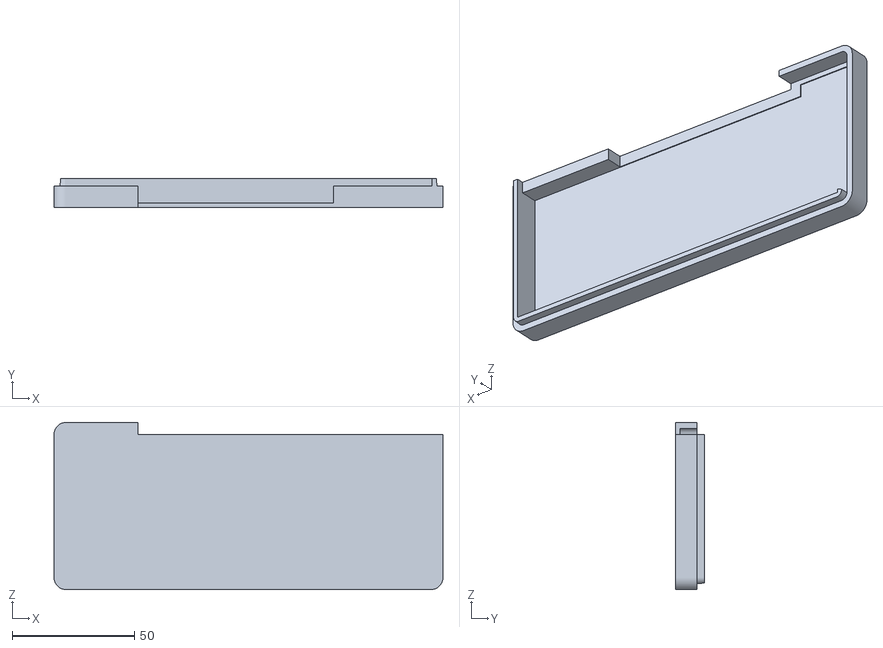
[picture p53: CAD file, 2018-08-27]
Hardware/Models/Control_Cover - Spacer.stl
159.3 x 11.8 x 68.5

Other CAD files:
Hardware/Models/MotorMount_BandSawr - Hall_Sensor_Cap.stl
Hardware/Models/MotorMount_BandSawr - Case.stl
Hardware/Models/MotorMount_BandSawr - Case End 1.stl
Hardware/Models/MotorMount_BandSawr - Case 2.stl

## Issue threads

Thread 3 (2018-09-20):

Adjusting arduino .ino file

seans883, 2018-09-20:
Is the sfm_slope defined in the .ino file what needs to be changed if i were to use this on a different size band saw? If so how did you calculate that number?

PotatoX, 2018-09-23:
Let me know if the additional instructions help resolve your issue. Once you confirm I will close out issue.

PotatoX, 2018-09-23:
Additional instruction are posted in the software  section.

PotatoX, 2018-09-29:
Close

Closed 2018-09-29.

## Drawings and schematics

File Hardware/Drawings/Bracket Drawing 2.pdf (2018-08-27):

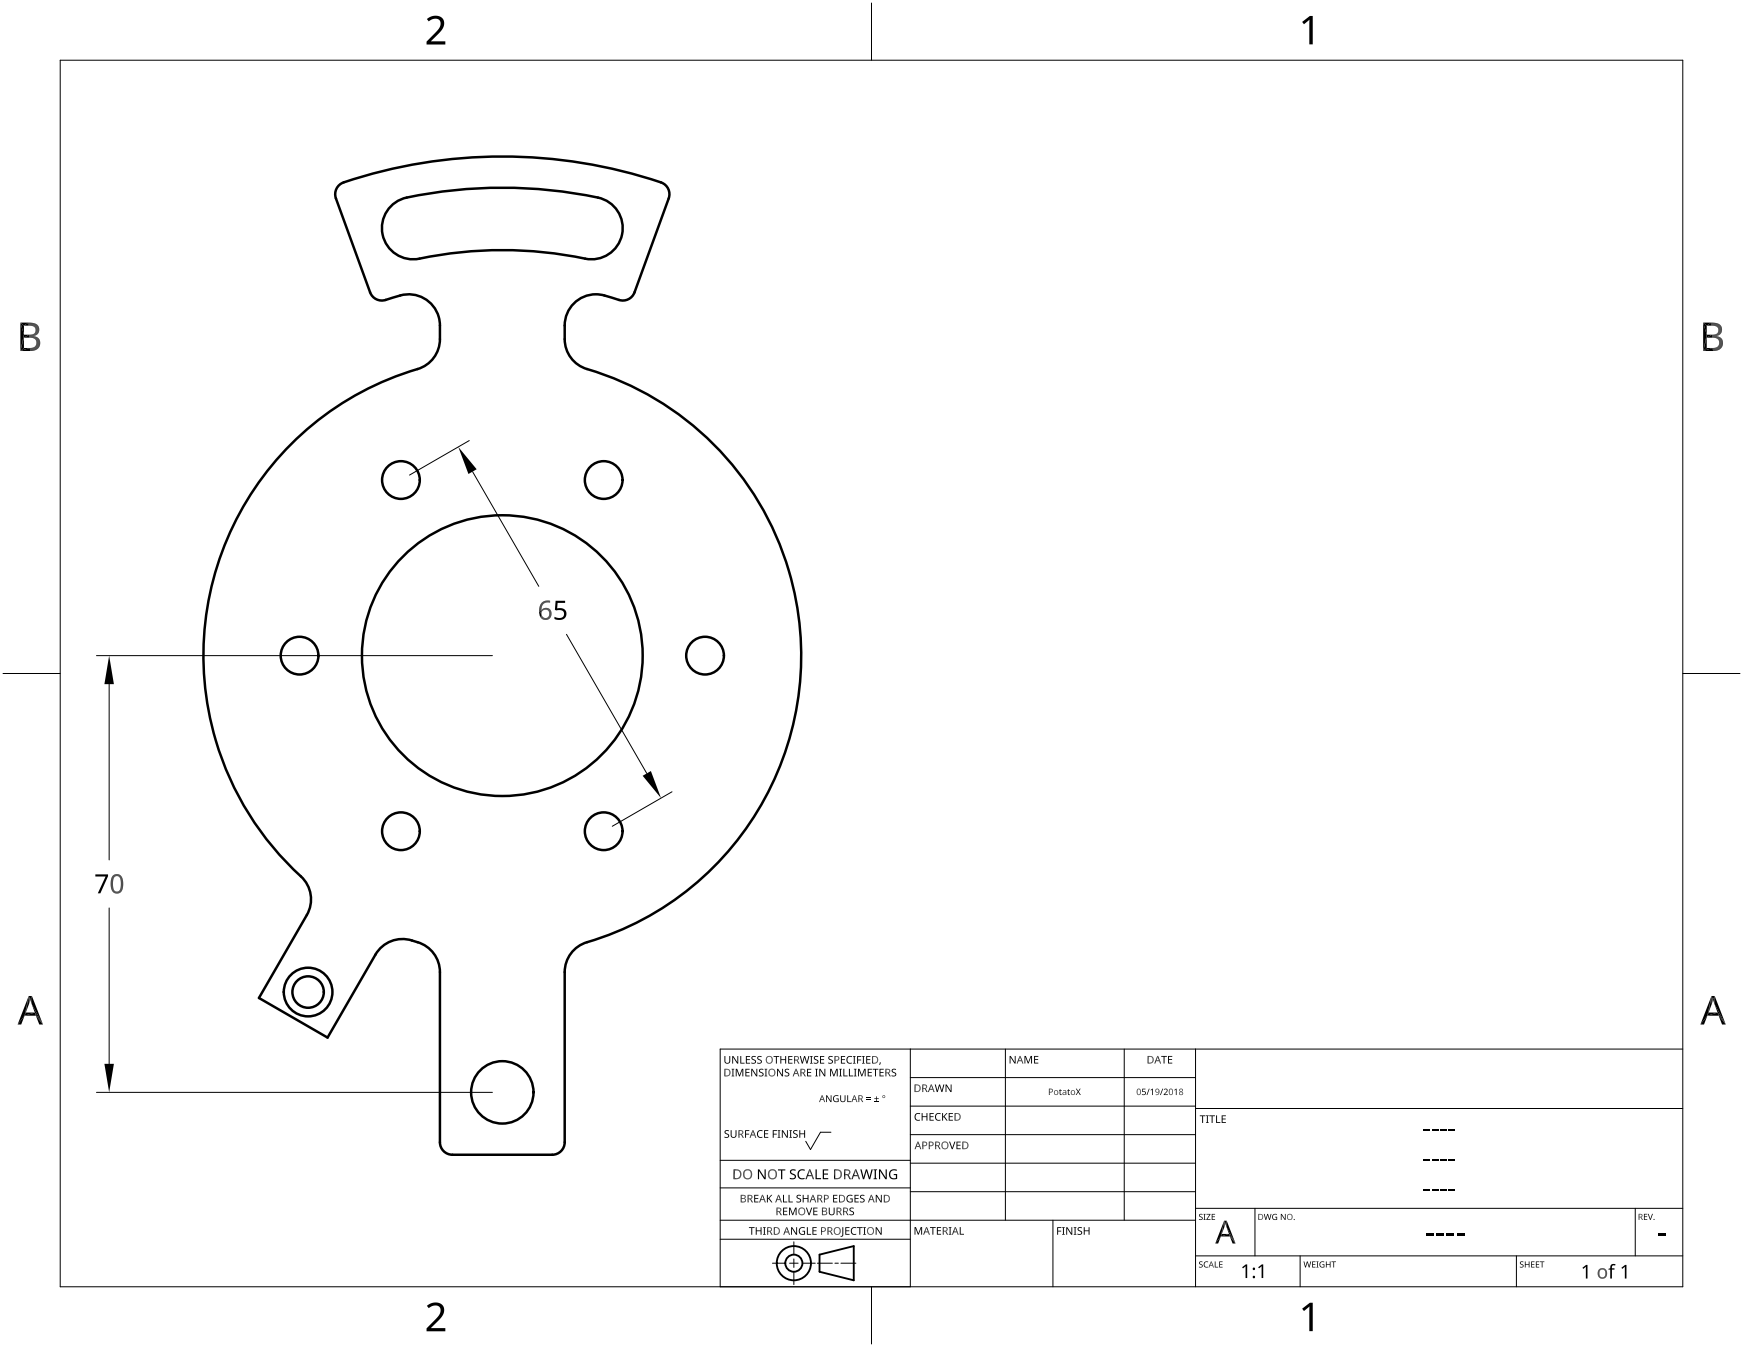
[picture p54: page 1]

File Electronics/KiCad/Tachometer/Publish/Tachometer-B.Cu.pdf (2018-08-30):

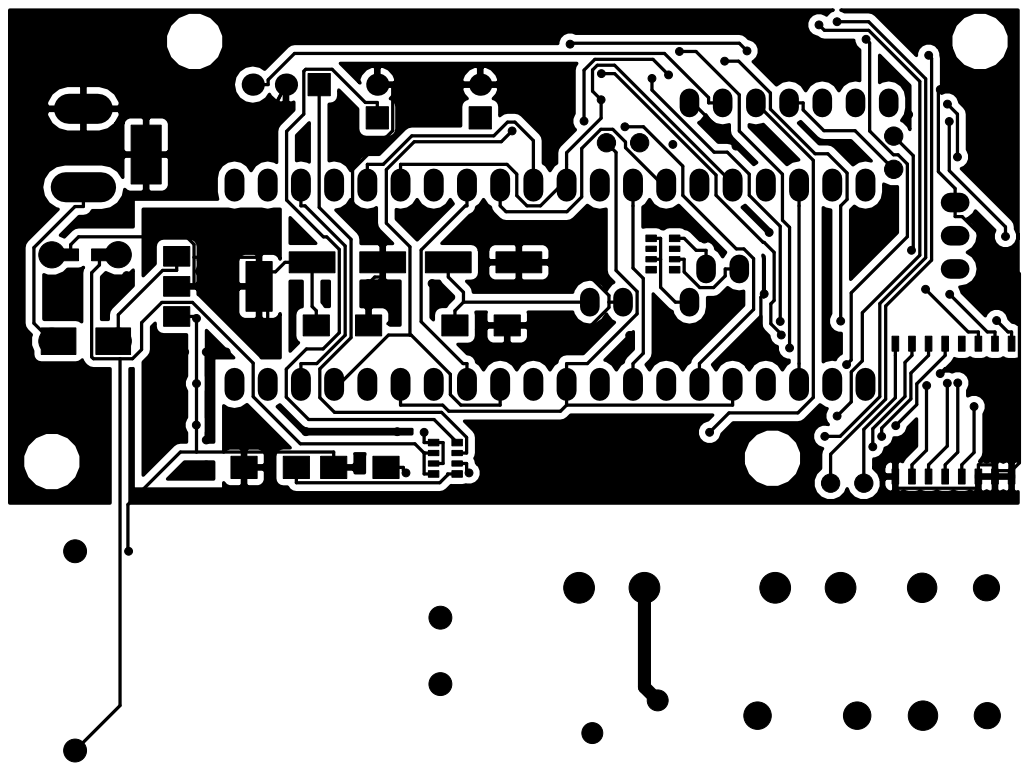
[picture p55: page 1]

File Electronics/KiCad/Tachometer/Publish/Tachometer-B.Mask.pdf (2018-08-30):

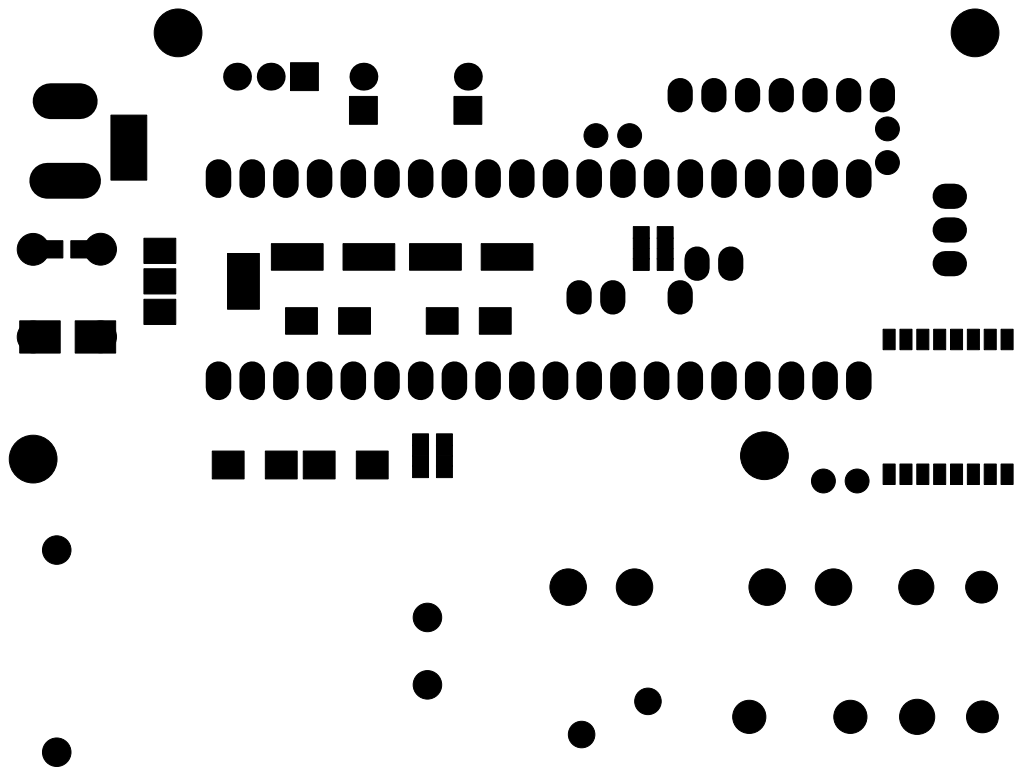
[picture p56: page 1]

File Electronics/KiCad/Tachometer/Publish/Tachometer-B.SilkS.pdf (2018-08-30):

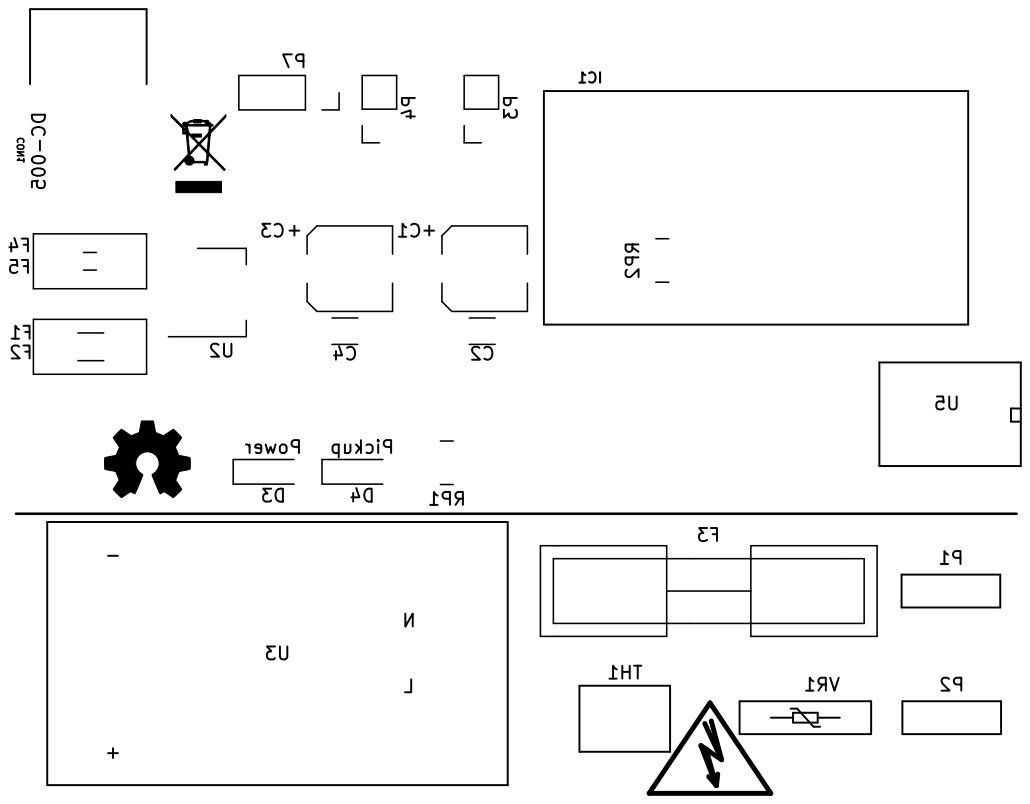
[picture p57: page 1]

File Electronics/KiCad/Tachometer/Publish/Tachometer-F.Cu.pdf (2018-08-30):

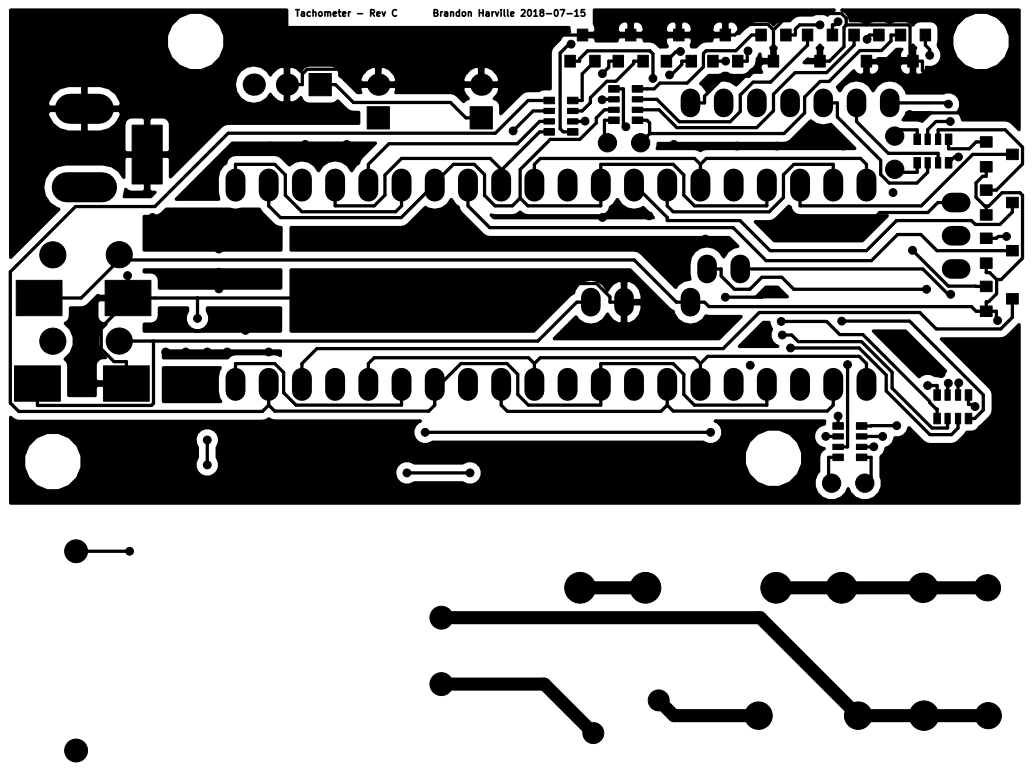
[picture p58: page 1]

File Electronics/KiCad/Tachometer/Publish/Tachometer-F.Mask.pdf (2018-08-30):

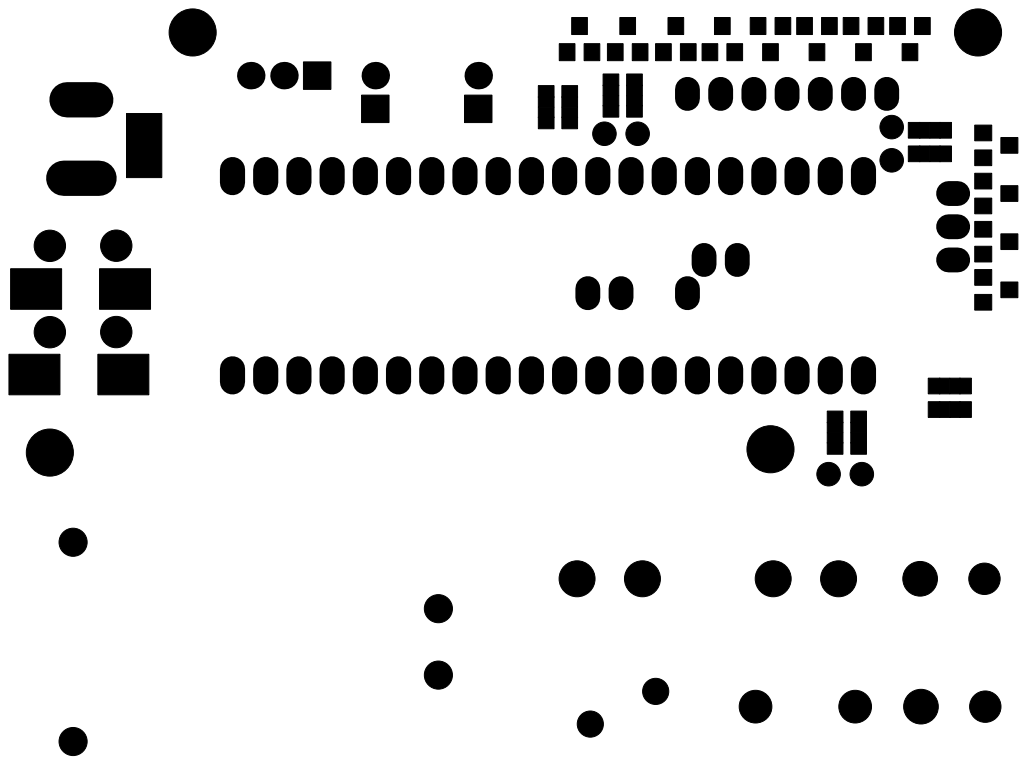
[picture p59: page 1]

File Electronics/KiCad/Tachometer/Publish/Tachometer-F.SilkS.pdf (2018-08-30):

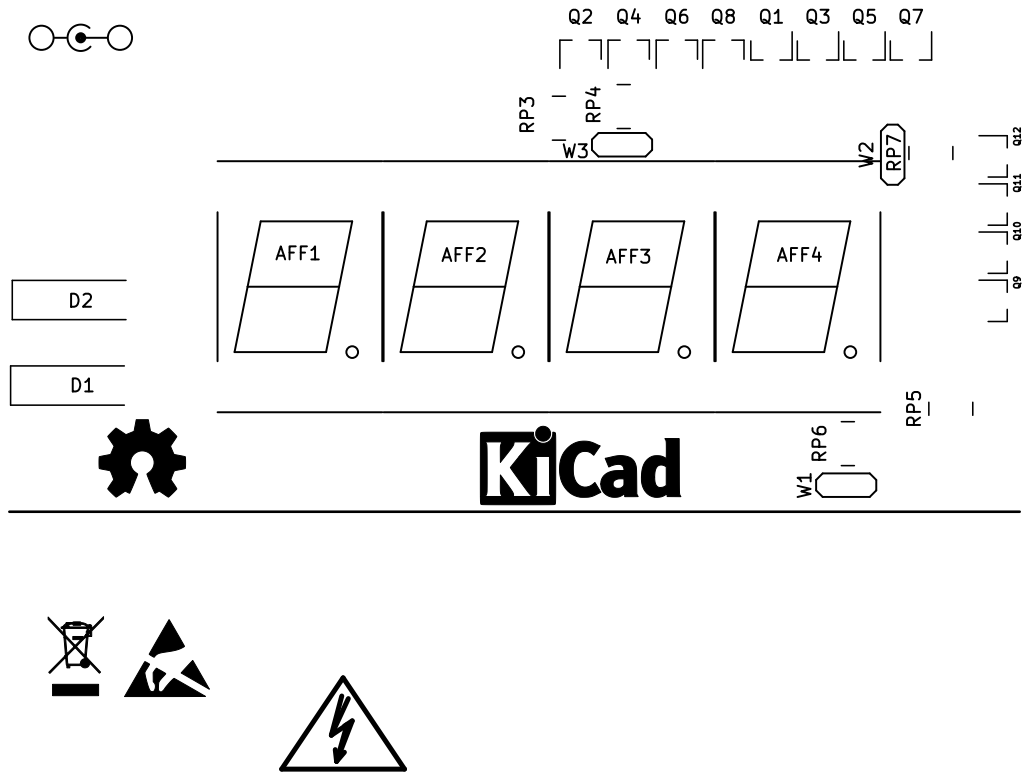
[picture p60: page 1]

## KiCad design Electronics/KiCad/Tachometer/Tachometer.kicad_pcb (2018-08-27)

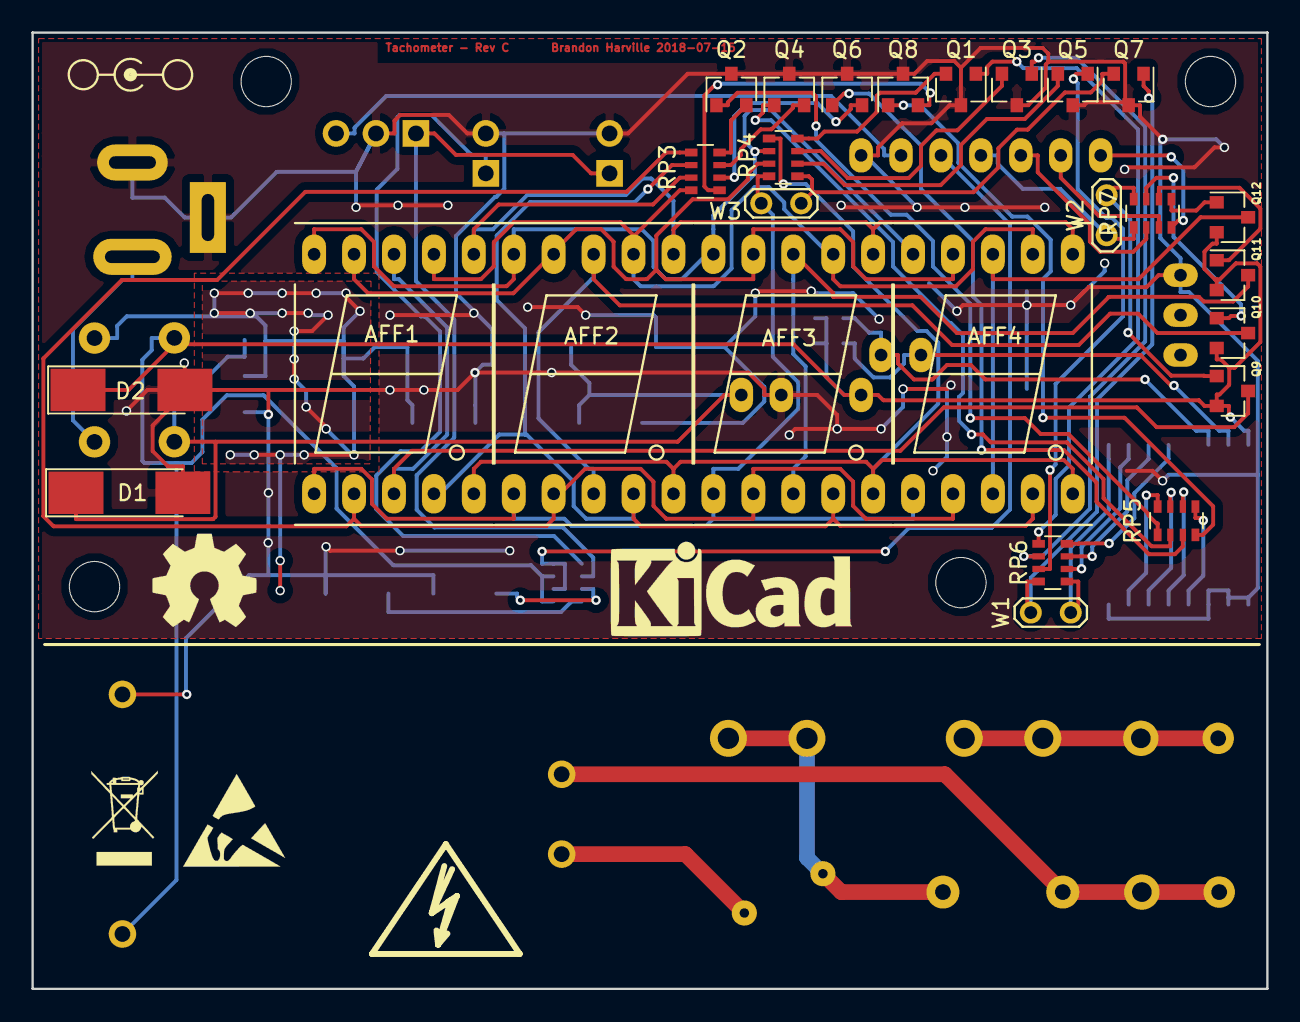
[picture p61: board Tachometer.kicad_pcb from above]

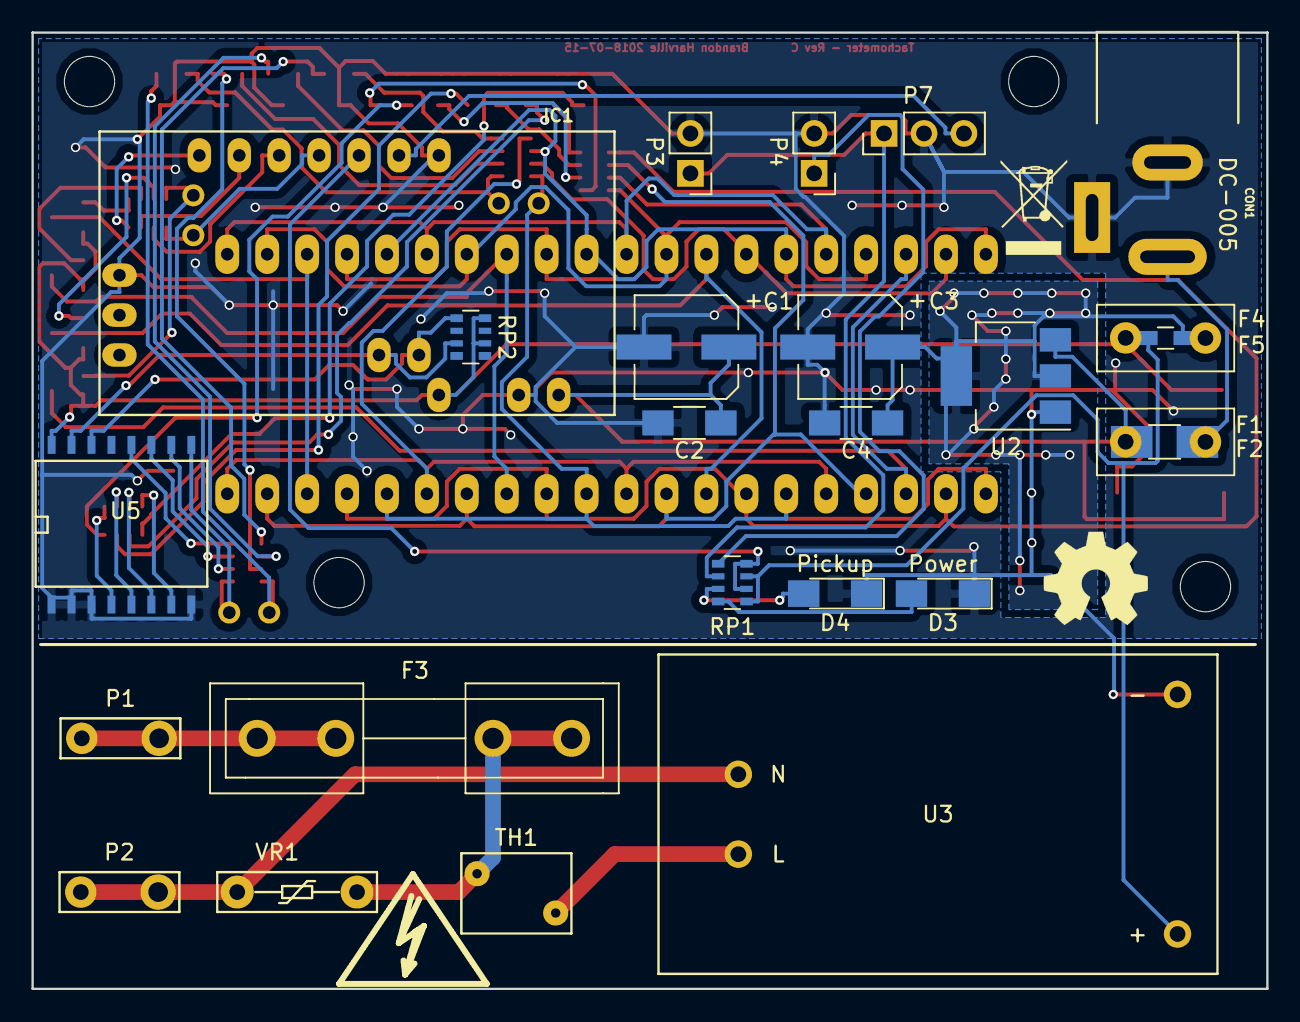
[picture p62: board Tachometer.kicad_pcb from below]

Board: 2 copper layers, 78.5 x 60.8 mm, 55 parts (25 on the bottom side), 61 nets.

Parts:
AFF1, AFF2, AFF3, AFF4: LTS-6960HR; 7SegmentLED_LTS6760_LTS6780
C1, C3: 10uF; CP_Elec_6.3x5.3
C2, C4: 22uF; C_1206_HandSoldering
CON1: DC-005; ADC-002
D1: 12V; D_MELF_Handsoldering
D2: 5.1V; D_MELF_Handsoldering
D3: Power; LED_1206_HandSoldering
D4: Pickup; LED_1206_HandSoldering
F1: 1A; Fuse_TE5_Littlefuse-395Series
F2: 2A 16V; Fuse_SMD1206_HandSoldering
F3: 1000mA; Fuseholder5x20_horiz_open_inline_Type-I
F4: 500mA; R_0603_HandSoldering
F5: 500mA; Fuse_TE5_Littlefuse-395Series
IC1: ArduinoProMini; pro_mini
M1, M2, M3, M4: MountingHole_3.2mm_M3_DIN965
P1, P2: CONN_01X01; Male_Terminal_Spade_Connector_6.3_Wide_5.08mm_Pins
P3, P4: CONN_01X02; Pin_Header_Straight_1x02_Pitch2.54mm
P7: CONN_01X03; Pin_Header_Straight_1x03_Pitch2.54mm
Q1, Q2, Q3, Q4, Q5, Q6, Q7, Q8, Q9, Q10, Q11, Q12: MMBT3906; SOT-23
RP1: 150; R_Array_Convex_4x0603
RP2: 10K; R_Array_Convex_4x0603
RP3, RP4: 91; R_Array_Convex_4x0603
RP5, RP6: 100; R_Array_Convex_4x0603
RP7: 510; R_Array_Convex_4x0603
TH1: NTC 5D-7; RV_Disc_D7_W5.1_P5
U2: LM1117-5.0; SOT-223-3_TabPin2
U3: TSP-05; TSP
U5: PCF8574; SO-16-W
VR1: 14D241K 240V; VARISTOR_MCIGICM_14D241K_240V
W1, W2, W3: TEST; Test_Point_2Pads

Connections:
/5V_REG: D2.1, F4.2, F5.2, IC1.21, Q9.2, Q10.2, Q11.2, Q12.2, RP1.1, RP1.3, RP2.2, RP2.4, U3.3, U5.16
/DC_IN: C1.1, C2.1, D1.1, F1.2, F2.2, IC1.24, U2.3
/GND: C1.2, C2.2, C3.2, C4.2, CON1.2, CON1.3, D1.2, D2.2, D3.1, D4.1, IC1.4, IC1.23, IC1.29, P3.2, P4.2, P7.2, Q1.3, Q2.3, Q3.3, Q4.3, Q5.3, Q6.3, Q7.3, Q8.3, U2.1, U3.4, U5.1, U5.2, U5.3, U5.8
/M_LIVE: F3.1, P1.1
/M_NEUTRAL: P2.1, U3.2, VR1.1
unnamed: AFF1.1, AFF2.1, AFF3.1, AFF4.1, RP4.8, W3.2
unnamed: AFF1.2, AFF2.2, AFF3.2, AFF4.2, RP3.5
unnamed: AFF1.3, AFF1.8, Q9.3
unnamed: AFF1.4, AFF2.4, AFF3.4, AFF4.4, RP3.6
unnamed: AFF1.5, AFF2.5, AFF3.5, AFF4.5, RP4.5
unnamed: AFF1.6, AFF2.6, AFF3.6, AFF4.6, RP3.7
unnamed: AFF1.7, AFF2.7, AFF3.7, AFF4.7, RP3.8
unnamed: AFF1.9, AFF2.9, AFF3.9, AFF4.9, RP4.7
unnamed: AFF1.10, AFF2.10, AFF3.10, AFF4.10, RP4.6
unnamed: AFF2.3, AFF2.8, Q10.3
unnamed: AFF3.3, AFF3.8, Q11.3
unnamed: AFF4.3, AFF4.8, Q12.3
unnamed: C3.1, C4.1, F4.1, F5.1, U2.2
unnamed: CON1.1, F1.1, F2.1
unnamed: D3.2, RP1.8
unnamed: D4.2, RP1.7
unnamed: F3.2, TH1.2, VR1.2
unnamed: IC1.5, P7.3
unnamed: IC1.6, RP1.2, RP1.4
unnamed: IC1.7, RP7.1, W2.1
unnamed: IC1.8, RP7.2
unnamed: IC1.9, RP7.3
unnamed: IC1.10, RP7.4
unnamed: IC1.25, RP2.7, U5.15
unnamed: IC1.26, RP2.5, U5.14
unnamed: P3.1, P7.1, RP1.6
unnamed: P4.1, RP1.5
unnamed: Q1.1, RP6.1
unnamed: Q1.2, RP4.4
unnamed: Q2.1, RP5.1
unnamed: Q2.2, RP3.4
unnamed: Q3.1, RP6.2
unnamed: Q3.2, RP4.3
unnamed: Q4.1, RP5.2
unnamed: Q4.2, RP3.3
unnamed: Q5.1, RP6.3
unnamed: Q5.2, RP4.2
unnamed: Q6.1, RP5.3
unnamed: Q6.2, RP3.2
unnamed: Q7.1, RP6.4, W1.1
unnamed: Q7.2, RP4.1, W3.1
unnamed: Q8.1, RP5.4
unnamed: Q8.2, RP3.1
unnamed: Q9.1, RP7.8, W2.2
unnamed: Q10.1, RP7.7
unnamed: Q11.1, RP7.6
unnamed: Q12.1, RP7.5
unnamed: RP5.5, U5.4
unnamed: RP5.6, U5.5
unnamed: RP5.7, U5.6
unnamed: RP5.8, U5.7
unnamed: RP6.5, U5.9, W1.2
unnamed: RP6.6, U5.10
unnamed: RP6.7, U5.11
unnamed: RP6.8, U5.12
unnamed: TH1.1, U3.1

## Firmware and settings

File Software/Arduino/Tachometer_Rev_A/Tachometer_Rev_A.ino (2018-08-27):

//---Streaming---//
  #include <Streaming.h>
//---Streaming---//

//---PCF8574---//
#include "PCF8574.h"
#include <Wire.h>

//PCF8574 PCF_01(0x38);
PCF8574 PCF_01(0x20);
//---PCF8574---//

// initialize global variable
  double RPM = 0;
  double SFM = 0;
  
// the setup function runs once when you press reset or power the board
void setup() {
  
  //initialize digital display on I2C
  PCF_01.begin();
  
  // initialize digital pin 2 as DETECTOR_PIN
  #define DEBUG false
  #define REFRESH_RATE 500 //updates per second
  
  #define DETECTOR_PIN 2
  #define LED_PIN 3
  #define DIGIT_COUNT 4
  #define LAST_DIGITAL_PIN 7
  #define DISPLAY_1_ENABLE_PIN 7
  #define DISPLAY_2_ENABLE_PIN 6
  #define DISPLAY_3_ENABLE_PIN 5
  #define DISPLAY_4_ENABLE_PIN 4
  #define SFM_SLOPE 1.0644
  pinMode(DETECTOR_PIN, INPUT_PULLUP);
  pinMode(DISPLAY_1_ENABLE_PIN, OUTPUT);
  pinMode(DISPLAY_2_ENABLE_PIN, OUTPUT);
  pinMode(DISPLAY_3_ENABLE_PIN, OUTPUT);
  pinMode(DISPLAY_4_ENABLE_PIN, OUTPUT);
  pinMode(LED_PIN, OUTPUT);

  // set digital display initial state
  digitalWrite(DISPLAY_1_ENABLE_PIN, HIGH);
  digitalWrite(DISPLAY_2_ENABLE_PIN, HIGH);
  digitalWrite(DISPLAY_3_ENABLE_PIN, HIGH);
  digitalWrite(DISPLAY_4_ENABLE_PIN, HIGH);

  // attach interput for detector
  attachInterrupt(digitalPinToInterrupt(DETECTOR_PIN), detectedPickup, FALLING);  

  // initialize serial communication at 115200 bits per second:
  Serial.begin(115200);
}

// the loop function runs over and over again forever
void loop() {
  // reset pickup led to LOW
  digitalWrite(LED_PIN, LOW);  

  // write out RPM to serial
  static unsigned long currentTime = millis();
  if(millis() - currentTime > 1.0/REFRESH_RATE/DIGIT_COUNT*1000)
  {
    currentTime = millis();

    // write RPM to serial    
    if( DEBUG )
    {
      RPM = 1234;
      Serial << "RPM: " << RPM << endl;  
    }

    // write out display serial  
    static int currentDigit = 1;
    static int lastDigit = DIGIT_COUNT;
    
    //disable digit  
    if( DEBUG )
      Serial << "Current Digit: " << currentDigit << endl;  

    //Convert RPM to SFM
    //RPM = 1000;
    SFM = RPM * SFM_SLOPE;
    
    //prepare current digit for display
    String RPMString;
    RPMString = (int) SFM;  
    RPMString = "0000" + RPMString;
    RPMString.remove(0,RPMString.length()-DIGIT_COUNT);
    if( DEBUG )
      Serial << "RPM String: " << RPMString << endl;
    RPMString = RPMString.charAt(DIGIT_COUNT - currentDigit);
    if( DEBUG )
      Serial << "RPM Char: " << RPMString << endl;
  
    //hide old digit
    digitalWrite(LAST_DIGITAL_PIN-lastDigit+1, HIGH);
    if( DEBUG )
      Serial << "Digital Pin " << LAST_DIGITAL_PIN-lastDigit+1 << ": HIGH" << endl;
      
    //write new digit        
    PCF_01.write8(~getDigit(RPMString.toInt()));
    //PCF_01.write8(~getDigit(currentDigit));
  
    //show new digit
    digitalWrite(LAST_DIGITAL_PIN-currentDigit+1, LOW);
    if( DEBUG )
      Serial << "Digital Pin " << LAST_DIGITAL_PIN-currentDigit+1 << ": LOW" << endl;
  
    //index and check digit count
    lastDigit = currentDigit;
    currentDigit += 1;
    if( currentDigit > DIGIT_COUNT )
      currentDigit = 1;  
  }

  // delay in between loop for stability
  if ( DEBUG )
    delay(1000);   
}

void detectedPickup()
{
  static unsigned long currentTime = millis();  
  static unsigned long lastTime = 0;

  // set the current time
  currentTime = millis();
  
  // setup array to store the last 10 values
  #define BUFFER_SIZE 10
  static unsigned long valueBuffer[BUFFER_SIZE] = {0};
  static int valueBufferPointer = 0;

  valueBuffer[valueBufferPointer] = currentTime - lastTime;

  // store the current time for use next cycle
  lastTime = currentTime;

  // average the buffer values
  unsigned long arraySum = 0;
  for(int i = 0; i < BUFFER_SIZE; i++)
  {
    arraySum += valueBuffer[i];
    if( DEBUG )
      Serial << "Array Value" << i + 1 << ": " << valueBuffer[i] << endl;
  }

  // calculate RPM (arrayAverage)
  double arrayAverage = arraySum / BUFFER_SIZE;

  // write RPM value to global variable
  RPM = 1000/arrayAverage*60;  
  if( DEBUG )
    Serial << "Buffer Pointer: " << valueBufferPointer << endl;

  // write pickup led HIGH
  digitalWrite(LED_PIN, HIGH);

  // reset pointer
  if (valueBufferPointer == BUFFER_SIZE - 1)
  {    
    valueBufferPointer = 0;
    if( DEBUG )
      Serial << "Buffer pointer reset." << endl;
  }
  else
  {
    valueBufferPointer += 1;
    if( DEBUG )
      Serial << "Increment pointer..." << endl;
  }
  
}

byte getDigit( int digit)
{
  #define DIGITAL_1 B00000110
  #define DIGITAL_2 B01011011
  #define DIGITAL_3 B01001111
  #define DIGITAL_4 B01100110
  #define DIGITAL_5 B01101101
  #define DIGITAL_6 B01111101
  #define DIGITAL_7 B00000111
  #define DIGITAL_8 B01111111
  #define DIGITAL_9 B01100111
  #define DIGITAL_0 B00111111 

  switch(digit)
  {
    case 0:
      return DIGITAL_0;
    
    case 1:
      return DIGITAL_1;
    
    case 2:
      return DIGITAL_2;
          
    case 3:
      return DIGITAL_3;
          
    case 4:
      return DIGITAL_4;
          
    case 5:
      return DIGITAL_5;
          
    case 6:
      return DIGITAL_6;
          
    case 7:
      return DIGITAL_7;
          
    case 8:
      return DIGITAL_8;
          
    case 9:
      return DIGITAL_9;
  }
}

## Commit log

2018-08-27 Intial uploads of project
    [Control_Cover - Cover_1.stl, Control_Cover - Cover_2.stl, Control_Cover - Cover_3.stl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]
2018-08-27 More initial uploads
    [SCR Controller Calc.xlsx, Tachometer - Rev A.sch, Tachometer - Rev B.sch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]
2018-08-30 More updates
    [BOM.xlsx]
2018-09-23 Slope Instruction
    [BandSaw Slope Calculations.ods, BandSaw Slope Calculations.xlsx]
